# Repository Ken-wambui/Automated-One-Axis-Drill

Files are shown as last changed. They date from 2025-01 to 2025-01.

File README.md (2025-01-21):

One-Axis Drill: Design and Fabrication

**Introduction**
Welcome to the One-Axis Drill project! This repository contains the design, fabrication, and implementation details for a one-axis automated drilling machine. The project is intended for students, hobbyists, and professionals interested in mechanical design, CNC machinery, and automation.

Project Overview
The One-Axis Drill is designed to automate the drilling process along a single axis, providing precision and repeatability. It integrates mechanical, electrical, and software components to achieve its goal.

**Features**
Precision Drilling: Accurate drilling along a single axis.
Automated Control: Programmed movements for consistent results.
Customizable Design: Easy to modify for different applications.
Open Source: All design files and source code are available for free.

Acknowledgements
We would like to thank the open-source community for their invaluable resources and support.

Contact
For any questions or suggestions, feel free to open an issue in this repository or contact us at kentrevor2@gmail.com.

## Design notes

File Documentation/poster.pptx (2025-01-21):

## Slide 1

GROUP MEMBERS
1. Elizabeth Mugure
2. Fernado Ghati
3. Edwin Maina
4. John Kabi
5. Randy Baraka
6. Kenneth Wambui

Development Of One Axis Drill

MAIN OBJECTIVE
Development of a precise automated one axis drill and determine optimal drilling parameters.
Specific Objectives
- To design and simulate 3D model of the physical system.
- To develop project circuits and firmware to run sensors, actuators and peripherals.
- To carry out preliminary experiments and analysis to determine parameters for vibration mitigation

EXPECTED OUTCOMES
- To have an efficient firmware program for the working of sensors, actuators and peripherals for precise drilling operation
- To establish optimal drilling parameters from experimental and computational analysis.
- To visualize forces and vibration on the PMMA with respect to drill and feed speeds
- To mitigate vibrations, chatter and reduced risk of drill bit breakage and ensure efficient material removal during drilling.

22nd Aug, 2023

Supervisor: Dr. Titus Mulembo

ABSTRACT
Many industrial and medical applications call for perfectly drilled holes. The creation of an affordable, accurate drilling machine that can be used and records vibrations and forces exerted on the workpiece throughout the drilling process is essential. This research aims to improve bone drilling operations in medical applications by developing a one-axis drill system with a polymer workpiece. In order to mitigate vibration and reduce chatter or the risk of drill bit breakage, system monitoring is crucial for identifying the optimal parameters to use in system control. This involves utilizing analytical and computational resources to analyze PMMA behavior during drilling operations and guaranteeing effective material removal.

METHODOLOGY

1. Assessment of existing physical model

2. Development of program flowchart

Determination of drilling control parameters
Upload the program to the microcontroller
Run the experiment
Results and Data Collection
Evaluation and analysis

3. CAD Design in Solidworks

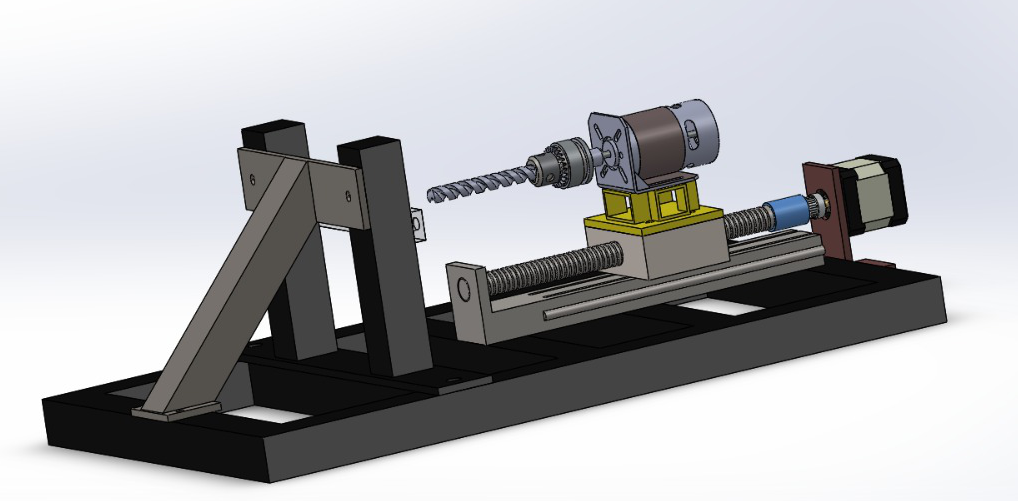
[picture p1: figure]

4. Importing to Matlab Simscape

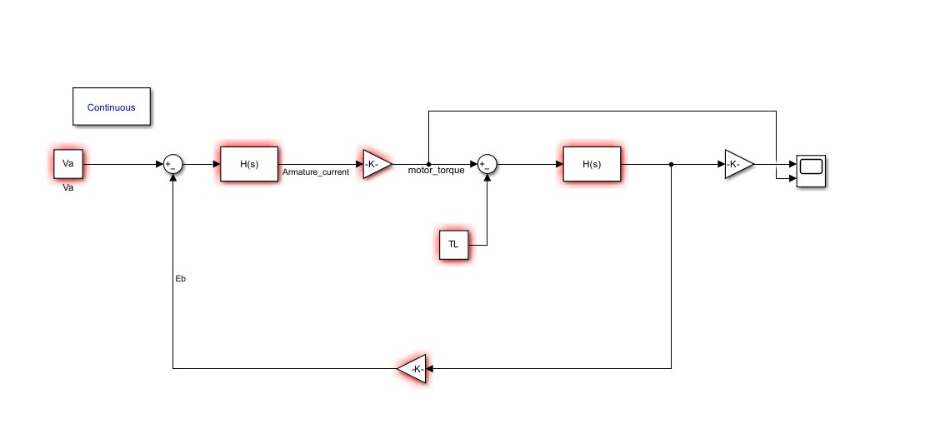
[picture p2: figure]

5. Finite element analysis in Ansys

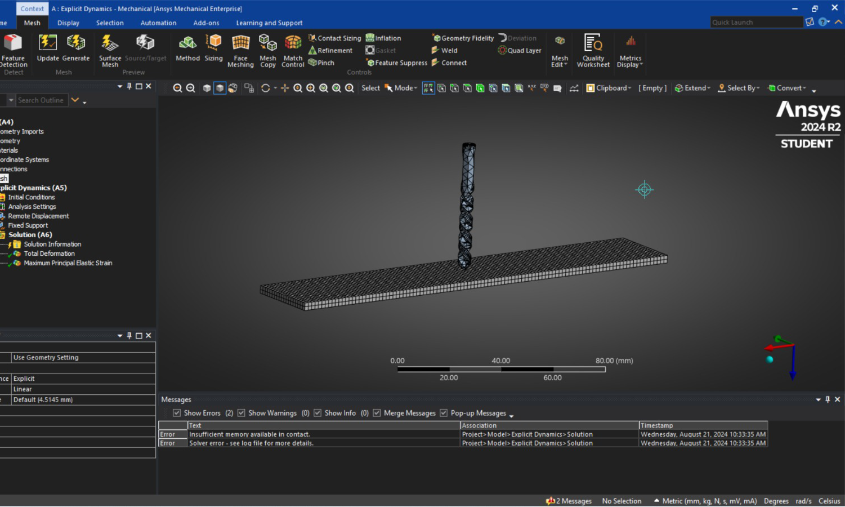
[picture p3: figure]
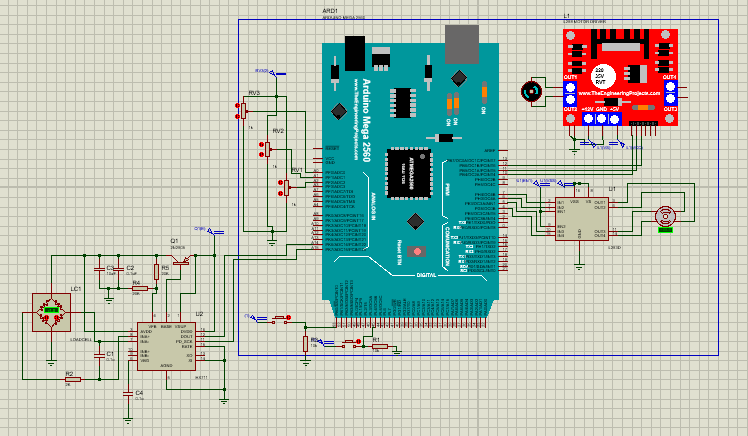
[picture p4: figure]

6. Programming and circuit simulation in Proteus, multisim

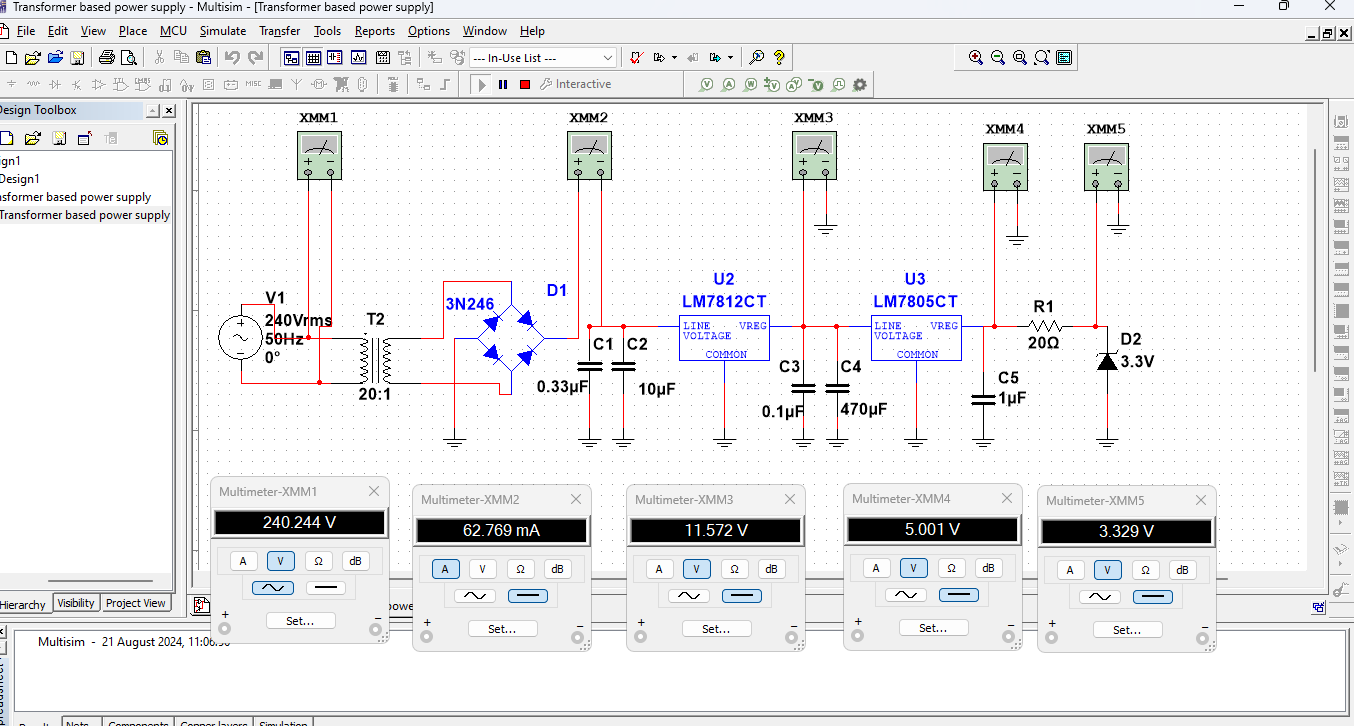
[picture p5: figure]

ACHIEVEMENTS

- Design of the project in Solidworks and simulation of the working motors in Matlab
- Circuit design in Proteus and simulations using Multism
- Development of working firmware program to read accurate real time sensor data and control dc and stepper motor.
- Gui Development for motor control and sensor data display

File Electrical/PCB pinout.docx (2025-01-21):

CIRCUIT PIN OUT

| Signal pin | Power pin
Stepper | B7(pul),A8(dir) | N/a
L298N dc motor control | B12(EN),B13(IN1),B14(IN2) | N/A
Vibration sensor | 10 | Pwr + gnd
Limit switch | A11 | Pwr + gnd
Temperature sensor | B8, B9
Load cell | B4, B5

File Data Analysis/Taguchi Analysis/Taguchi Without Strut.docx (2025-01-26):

WORKSHEET 1

Taguchi Analysis: Performance versus PWM, Feed Ratio, Diameter

Response Table for Signal to Noise Ratios

Larger is better

Level | PWM | Feed Ratio | Diameter
1 | 23.95 | 23.90 | 23.73
2 | 23.73 | 23.78 | 23.95
Delta | 0.23 | 0.13 | 0.23
Rank | 2 | 3 | 1

Response Table for Means

Level | PWM | Feed Ratio | Diameter
1 | 15.78 | 15.69 | 15.36
2 | 15.37 | 15.45 | 15.78
Delta | 0.41 | 0.23 | 0.42
Rank | 2 | 3 | 1

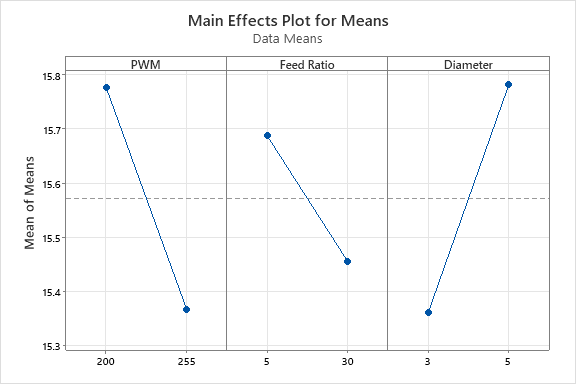
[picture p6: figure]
Main Effects Plot for Means
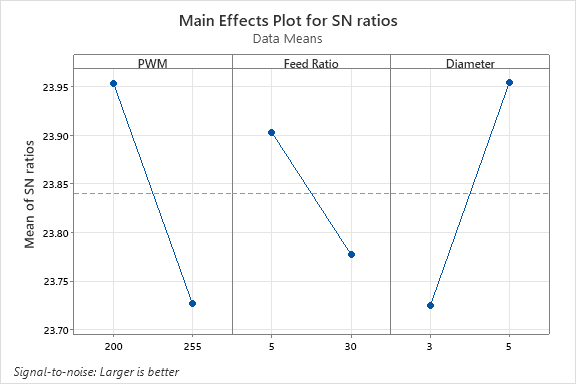
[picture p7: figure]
Main Effects Plot for SN ratios

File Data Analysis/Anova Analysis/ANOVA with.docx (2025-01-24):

Descriptive statistics

SHEET1

General Linear Model: Performance versus PWM, Feed Ratio,

WORKSHEET 1

General Linear Model: Performance versus PWM, Feed Ratio, Diameter

Method

Factor coding | (-1, 0, +1)

Factor Information

Factor | Type | Levels | Values
PWM | Fixed | 2 | 200, 255
Feed Ratio | Fixed | 2 | 5, 30
Diameter | Fixed | 2 | 3, 5

Analysis of Variance

Source | DF | Adj SS | Adj MS | F-Value | P-Value
PWM | 1 | 0.3351 | 0.3351 | 0.65 | 0.464
Feed Ratio | 1 | 0.1075 | 0.1075 | 0.21 | 0.671
Diameter | 1 | 0.3529 | 0.3529 | 0.69 | 0.453
Error | 4 | 2.0510 | 0.5127
Total | 7 | 2.8464

Model Summary

S | R-sq | R-sq(adj) | R-sq(pred)
0.716064 | 27.95% | 0.00% | 0.00%

Coefficients

Term | Coef | SE Coef | T-Value | P-Value | VIF
Constant | 15.571 | 0.253 | 61.50 | 0.000
PWM
200 | 0.205 | 0.253 | 0.81 | 0.464 | 1.00
Feed Ratio
5 | 0.116 | 0.253 | 0.46 | 0.671 | 1.00
Diameter
3 | -0.210 | 0.253 | -0.83 | 0.453 | 1.00

Regression Equation

Performance | = | 15.571 + 0.205 PWM_200 - 0.205 PWM_255 + 0.116 Feed Ratio_5 - 0.116 Feed Ratio_30 - 0.210 Diameter_3 + 0.210 Diameter_5

Diameter

Method

Factor coding | (-1, 0, +1)

Factor Information

Factor | Type | Levels | Values
PWM | Fixed | 2 | 200, 255
Feed Ratio | Fixed | 2 | 5, 30
Diameter | Fixed | 2 | 3, 5

Analysis of Variance

Source | DF | Adj SS | Adj MS | F-Value | P-Value
PWM | 1 | 0.74118 | 0.74118 | 1.03 | 0.367
Feed Ratio | 1 | 0.01561 | 0.01561 | 0.02 | 0.890
Diameter | 1 | 0.32520 | 0.32520 | 0.45 | 0.538
Error | 4 | 2.86852 | 0.71713
Total | 7 | 3.95051

Model Summary

S | R-sq | R-sq(adj) | R-sq(pred)
0.846835 | 27.39% | 0.00% | 0.00%

Coefficients

Term | Coef | SE Coef | T-Value | P-Value | VIF
Constant | 16.478 | 0.299 | 55.04 | 0.000
PWM
200 | 0.304 | 0.299 | 1.02 | 0.367 | 1.00
Feed Ratio
5 | 0.044 | 0.299 | 0.15 | 0.890 | 1.00
Diameter
3 | -0.202 | 0.299 | -0.67 | 0.538 | 1.00

Regression Equation

Perfomance | = | 16.478 + 0.304 PWM_200 - 0.304 PWM_255 + 0.044 Feed Ratio_5 - 0.044 Feed Ratio_30 - 0.202 Diameter_3 + 0.202 Diameter_5

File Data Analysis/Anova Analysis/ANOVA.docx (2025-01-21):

ANALYSIS OF VARIANCE(ANOVA)

1. Data collection

The goal of this analysis is to obtain optimal operating points for vibration and force on the workpiece and DC motor which provides rotary feed to the workpiece. We operate the DC under different conditions such as different drill bit sizes, different feed rate and drill speed to obtain optimal parameters for drilling PMMA material which mimic the properties of bones, which is a typical application of our project.

The two hypotheses in the experiment:

Null hypothesis: There is no significant difference in the mean quality of drilling across different levels of linear feed speed provided by the stepper motor and rotary speed determined by the DC motor.

Alternative hypothesis: There is a significant difference in the mean quality of drilling across different levels of linear feed speed provided by the stepper motor and rotary speed determined by the DC motor.

2. Interpretation of ANOVA results
- The p-values indicate the significance of each factor and their interactions.
- Feed rate has a p-value of <0.05, indicating that it has a significant effect on Optimal Drilling Performance.
- Drill Motor Speed also has a p-value of <0.05, suggesting a significant effect on Optimal Drilling Performance.
- Both the stepper motor speed and the drill motor speed independently significantly impact the quality or efficiency of the drilling process for PMMA material.
- The interaction between Stepper Motor Speed and Drill Motor Speed has a p-value of 0.516708, which is not statistically significant. Therefore, the interaction does not have a significant effect on Optimal Drilling Performance.
- The p- value of interaction between stepper motor speed and dc motor speed is greater than 0.5, thus we fail to reject null hypothesis; this means there is no significant difference in the mean quality of drilling across different levels of linear feed speed provided by the stepper motor and rotary speed determined by the DC motor. This means that the two variables can be controlled independent of each other to obtain best quality drilling.

From the analysis, the number of times the station is able to carry out a successful drilling operation is limited. The station exhibits a successful drilling operation when a slow feed rate and a fast drill speed is applied also when we have a smaller drill bits. Failure to drill can be attributed to the melting of PMMA and the sticking of the melted PMMA on the drill bit, making further drilling difficult. The new PMMA used melts when heated during heating. Using the current setup as it is, the optimal operating parameters is at Slow feed rate setting for stepper motor, where it operates at 21.6 rpm and for the dc motor, at 255PWM, which is equivalent to 9778rpm, which can be conditioned separately, with one of the variables held constant.

Recommendations

Since we’re using a relatively bigger motor, we should use a power supply that will provide supply of up to 24V for the DC motor to increase torque when drilling with bigger drill bits.

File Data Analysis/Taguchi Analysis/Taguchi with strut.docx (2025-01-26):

WORKSHEET 4

Taguchi Analysis: Perfomance versus RPM, Feed Ratio, Diameter

Response Table for Signal to Noise Ratios

Larger is better

Level | RPM | Feed Ratio | Diameter
1 | 24.49 | 24.35 | 24.22
2 | 24.17 | 24.31 | 24.44
Delta | 0.33 | 0.04 | 0.22
Rank | 1 | 3 | 2

Response Table for Means

Level | RPM | Feed Ratio | Diameter
1 | 16.78 | 16.52 | 16.28
2 | 16.17 | 16.43 | 16.68
Delta | 0.61 | 0.09 | 0.40
Rank | 1 | 3 | 2

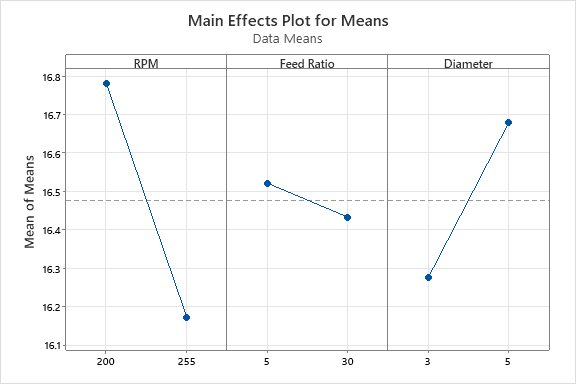
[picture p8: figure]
Main Effects Plot for Means
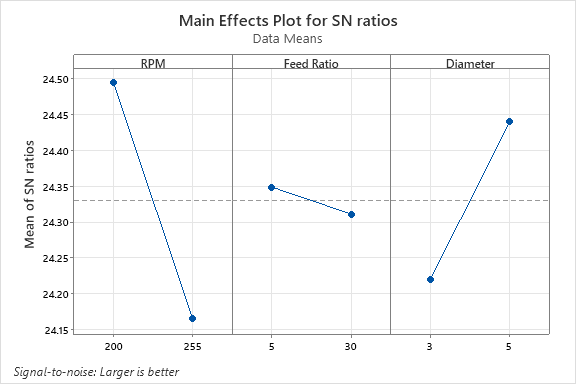
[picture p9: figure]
Main Effects Plot for SN ratios

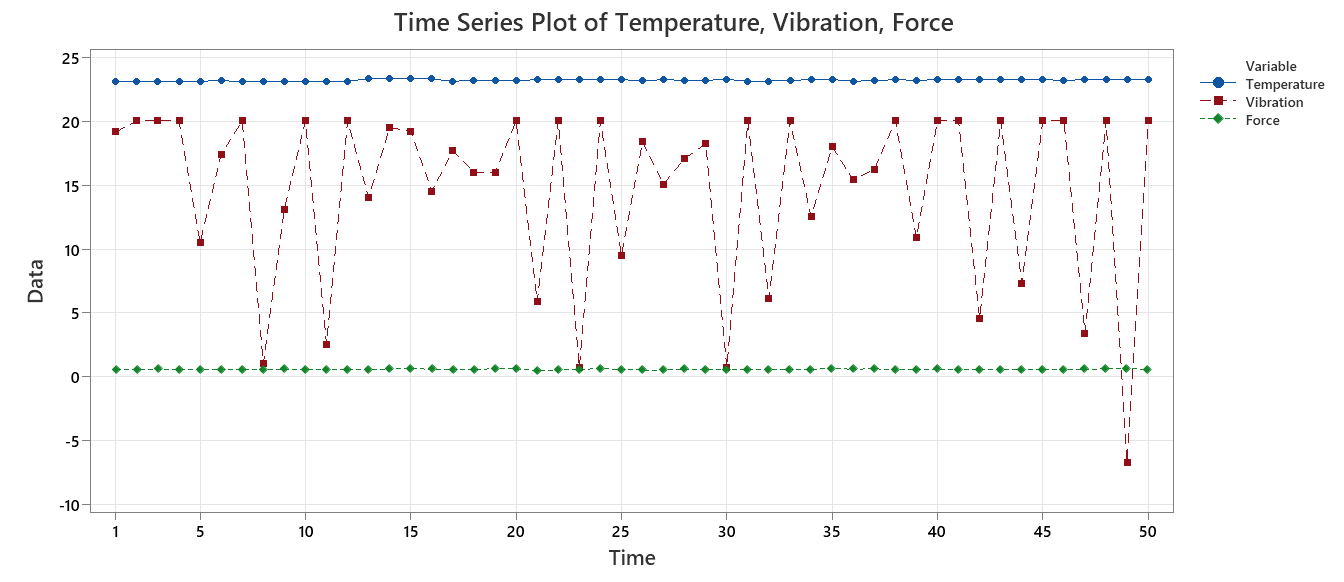
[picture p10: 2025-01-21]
Data Analysis/Graphs/Without Strut/5mm Bit/slow feed fast drill.png

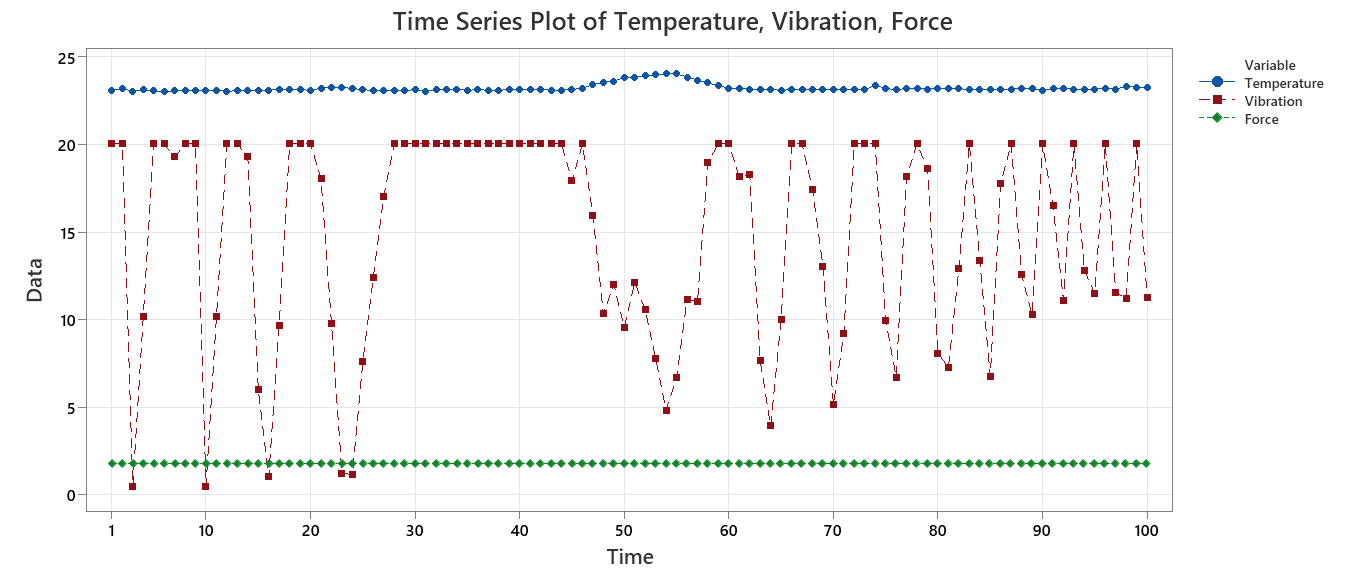
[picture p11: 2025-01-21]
Data Analysis/Graphs/Without Strut/3mm Bit/slow feed fast drill.png

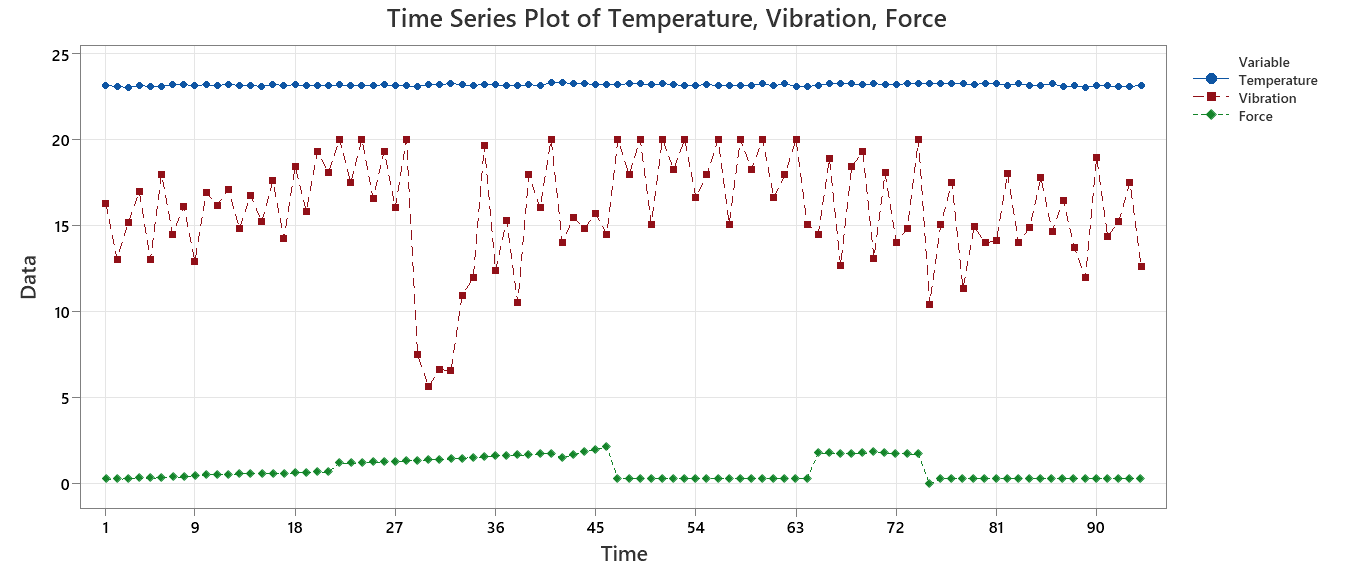
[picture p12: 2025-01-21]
Data Analysis/Graphs/Without Strut/3mm Bit/slow feed slow drill.png

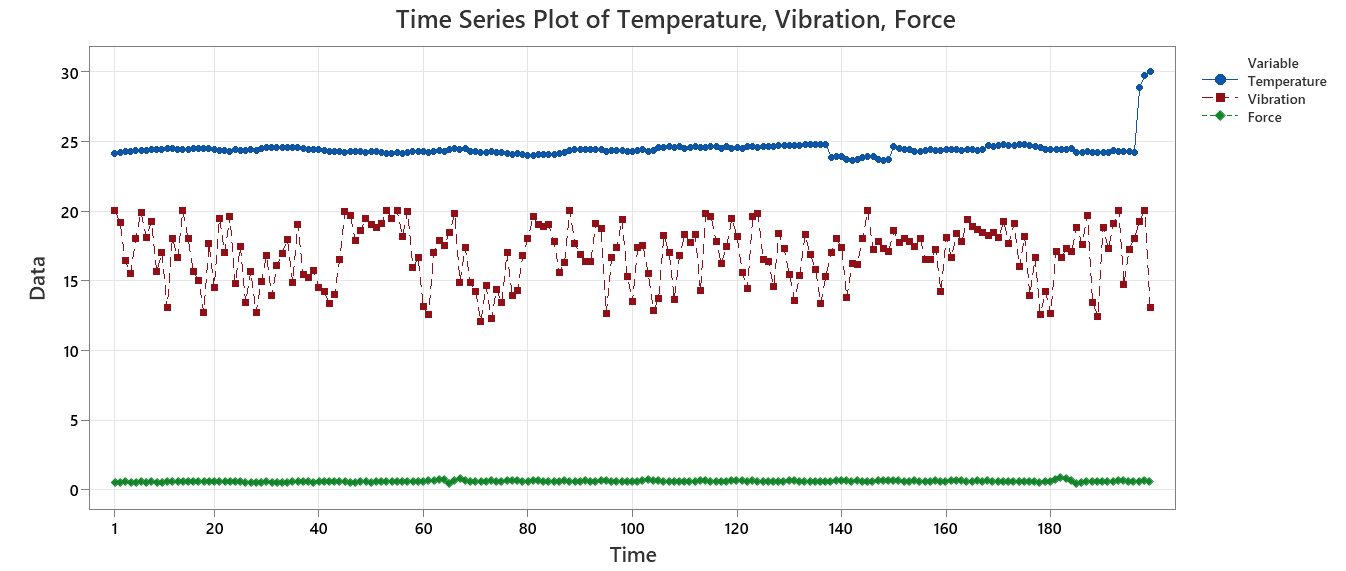
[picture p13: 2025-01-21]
Data Analysis/Graphs/With Strut/5mm Bit/slow feed fast drill.png

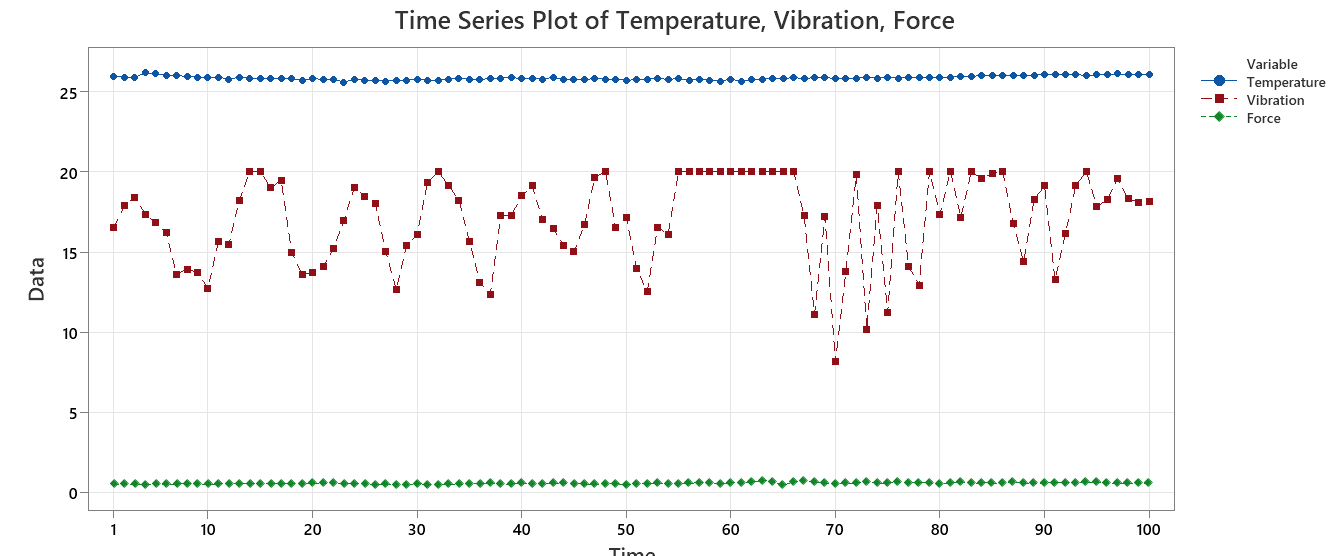
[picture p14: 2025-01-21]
Data Analysis/Graphs/With Strut/5mm Bit/Slow feed slow drill.png

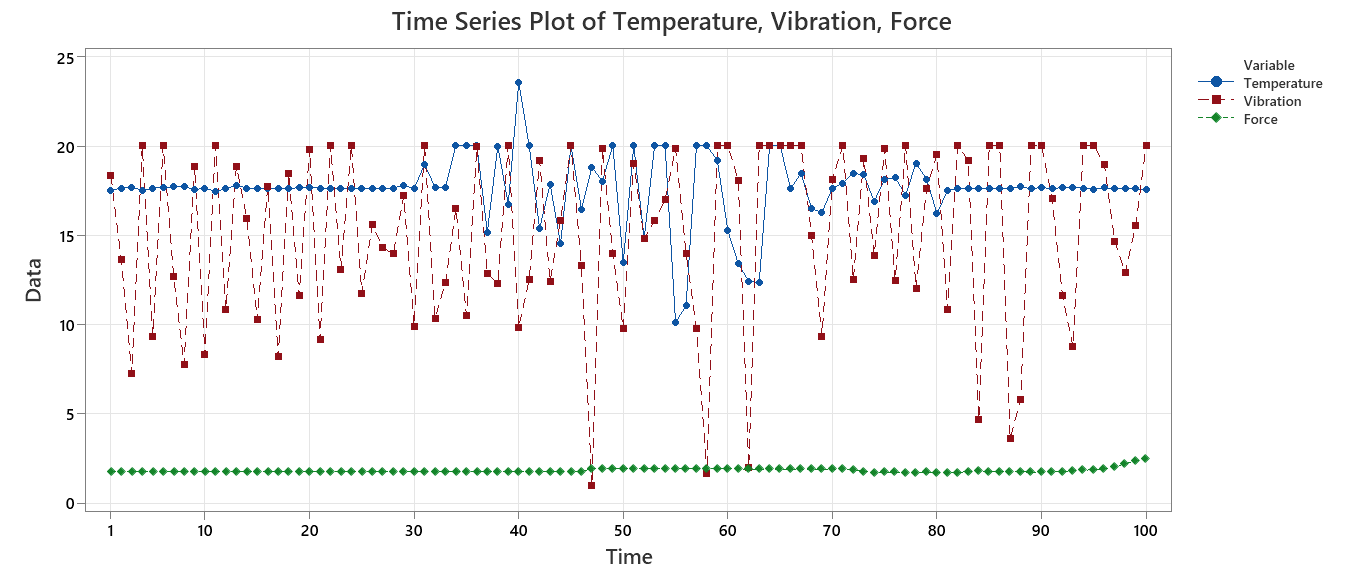
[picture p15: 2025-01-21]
Data Analysis/Graphs/With Strut/3mm Bit/fast feed slow drill.png

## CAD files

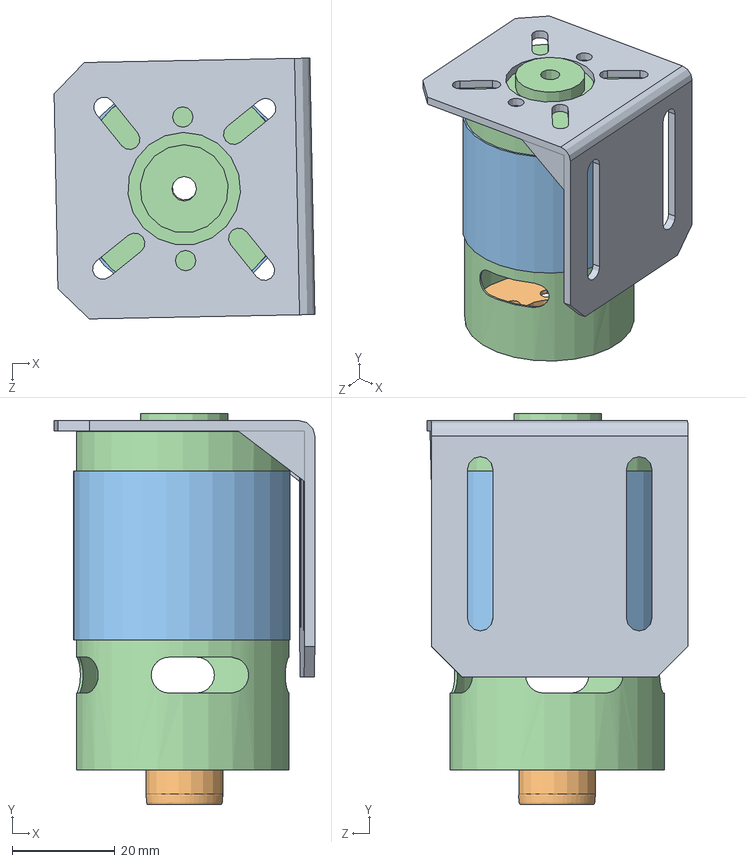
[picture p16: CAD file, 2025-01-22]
CAD/DC MOTOR/Assem2.SLDASM
50.9 x 76.2 x 50.9 mm
motor
case1
bottom
Motor Mount

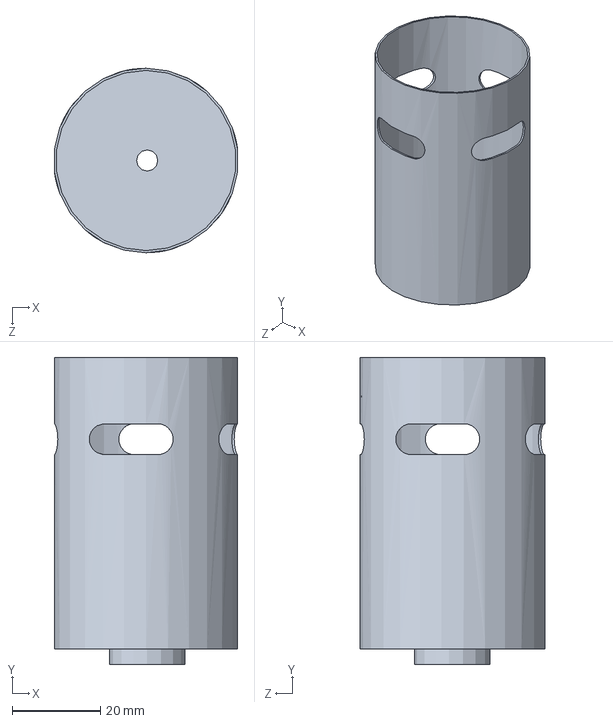
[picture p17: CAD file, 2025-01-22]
CAD/DC MOTOR/motor.SLDPRT
41.5 x 69.5 x 41.8 mm

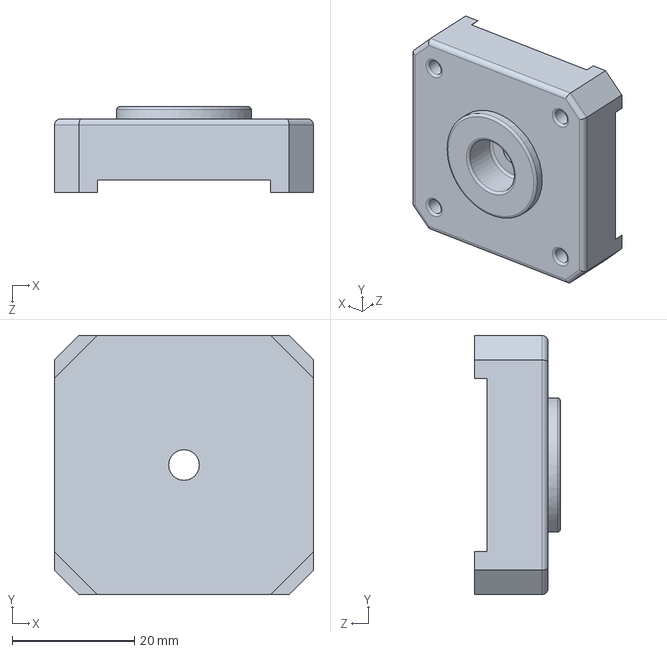
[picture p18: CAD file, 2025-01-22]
CAD/STEPPER MOTOR/Base Plate.SLDPRT
42.3 x 42.3 x 14.0 mm

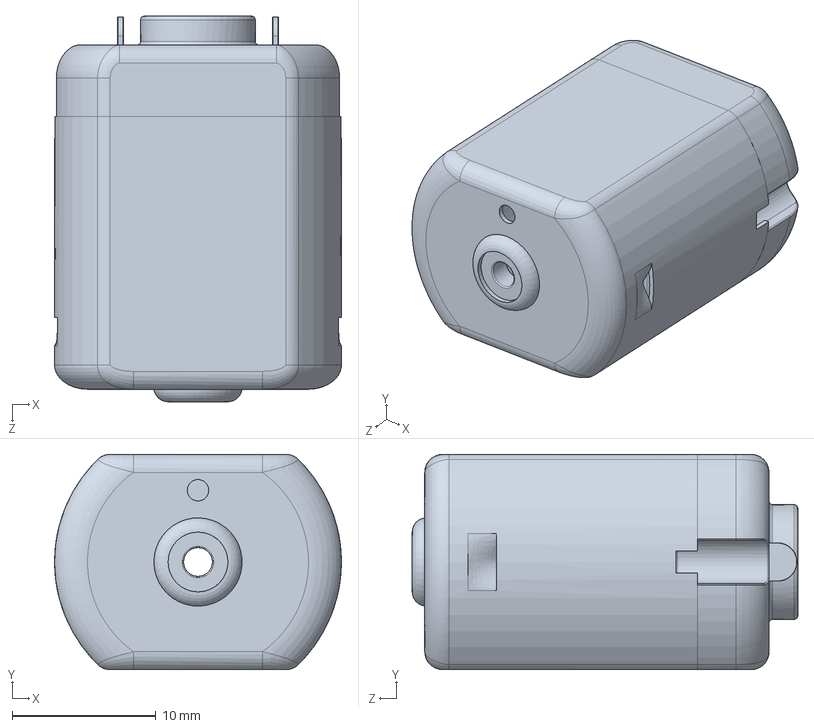
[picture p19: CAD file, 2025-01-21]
Simulations/Matlab/Dc motor/cassing.SLDPRT
20.0 x 15.0 x 26.9 mm

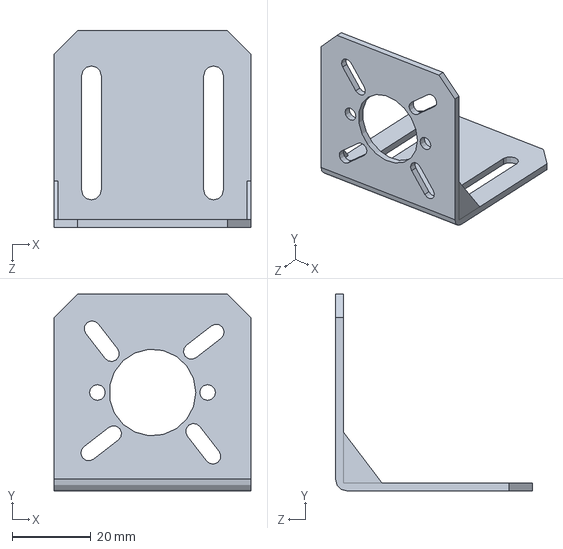
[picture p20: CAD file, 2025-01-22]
CAD/DC MOTOR/Motor Mount.SLDPRT
50.0 x 50.0 x 50.0 mm

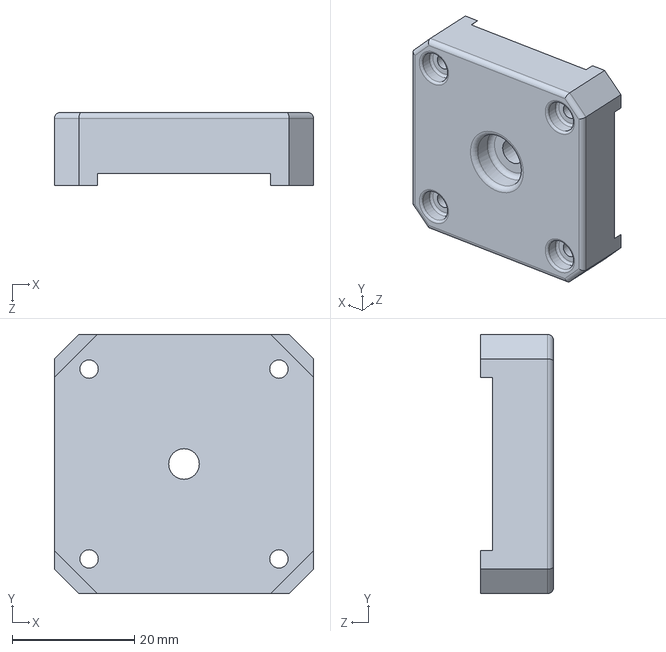
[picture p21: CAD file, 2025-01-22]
CAD/STEPPER MOTOR/Base step.SLDPRT
42.3 x 42.3 x 12.0 mm

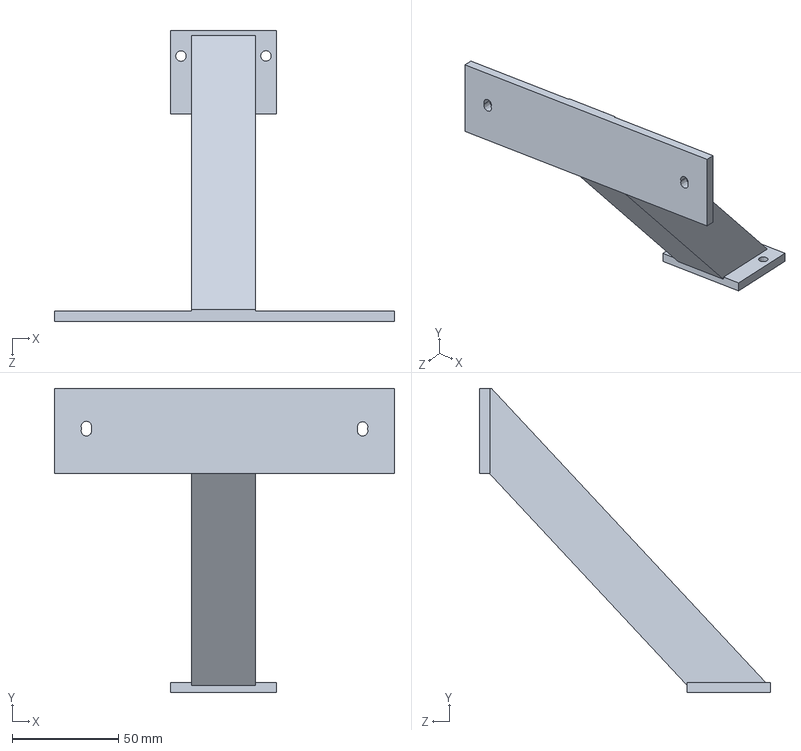
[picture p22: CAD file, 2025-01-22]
CAD/Strut.SLDPRT
160.0 x 143.3 x 136.9 mm

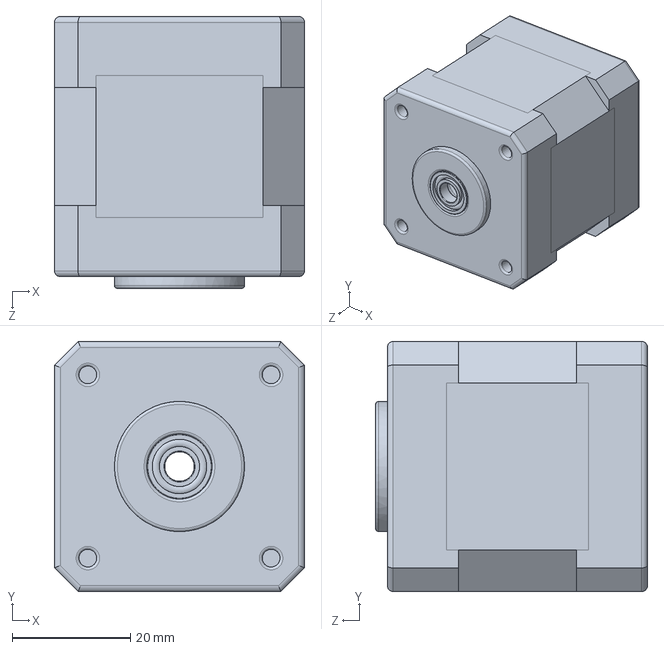
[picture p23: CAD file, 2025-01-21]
Simulations/Matlab/Stepper motor/case.SLDPRT
42.3 x 42.3 x 46.0 mm

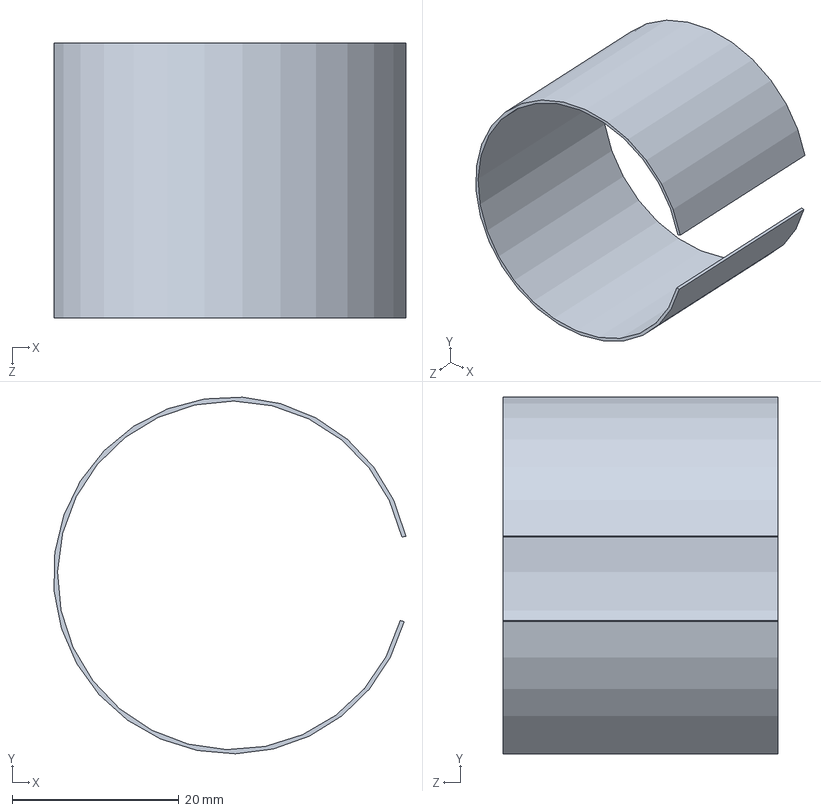
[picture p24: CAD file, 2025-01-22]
CAD/DC MOTOR/case1.SLDPRT
42.2 x 42.8 x 33.0 mm

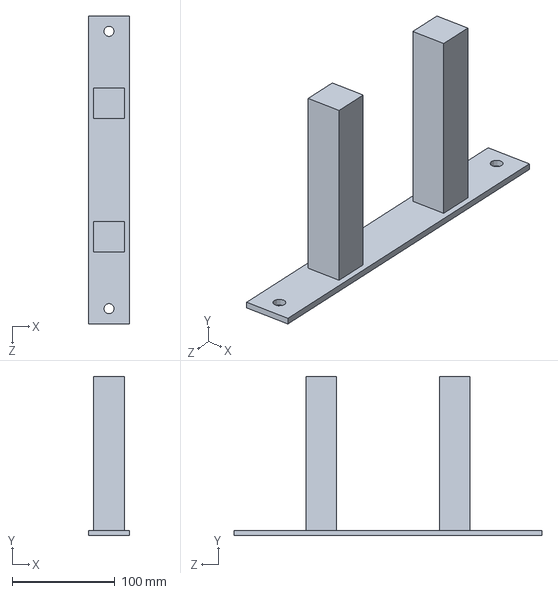
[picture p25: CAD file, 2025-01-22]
CAD/MOUNT.SLDPRT
40.0 x 155.0 x 300.0 mm

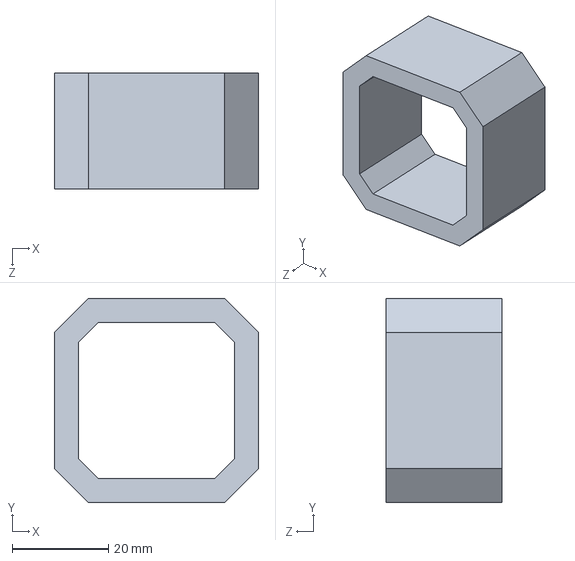
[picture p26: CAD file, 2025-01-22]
CAD/STEPPER MOTOR/Body.SLDPRT
42.3 x 42.3 x 24.0 mm

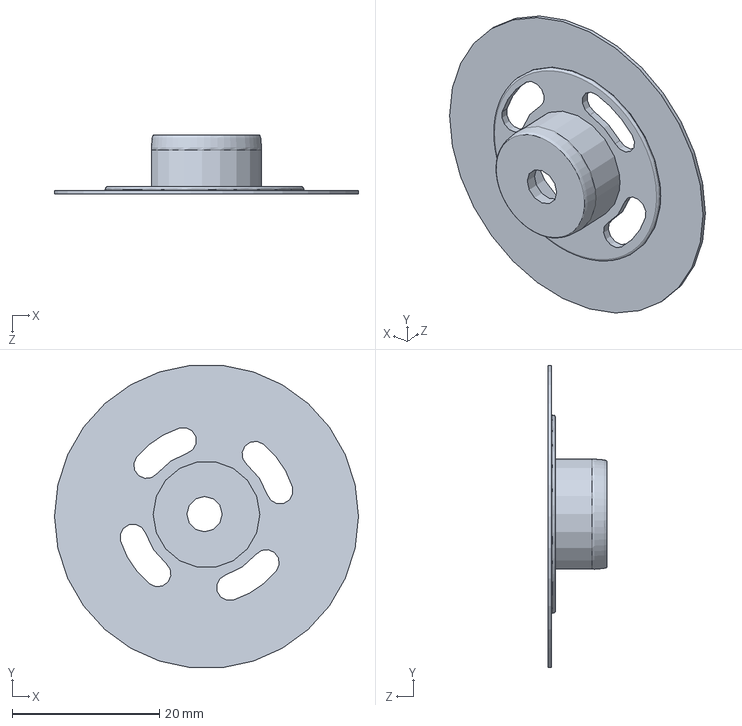
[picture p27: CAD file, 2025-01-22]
CAD/DC MOTOR/bottom.SLDPRT
41.3 x 41.1 x 8.00 mm

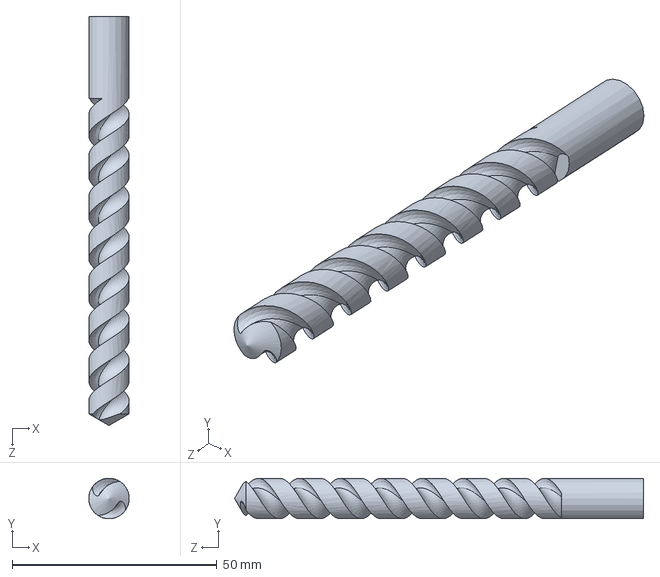
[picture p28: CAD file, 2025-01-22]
CAD/Drill Bit.SLDPRT
9.90 x 9.90 x 100.0 mm

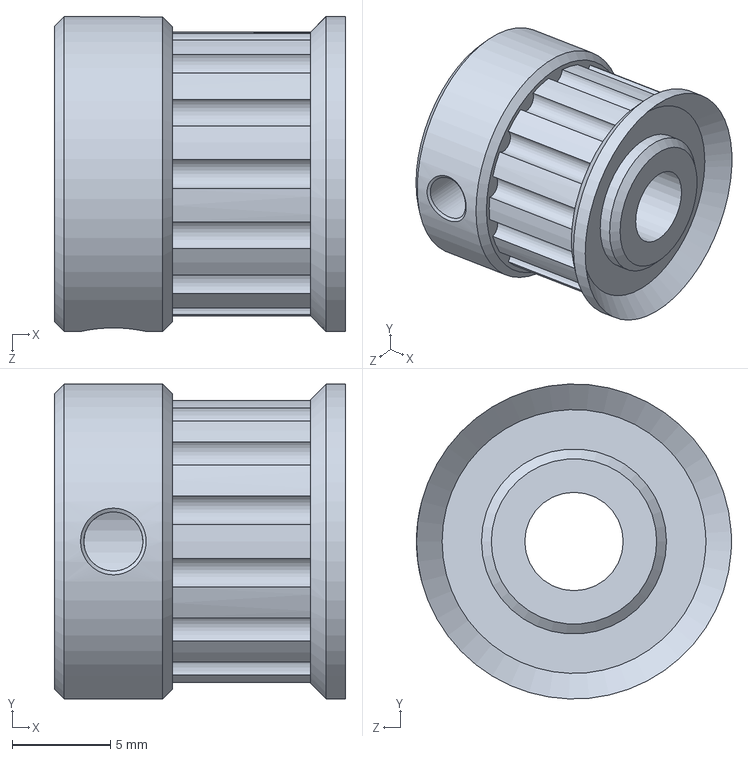
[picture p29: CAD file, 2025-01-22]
CAD/STEPPER MOTOR/Pulley.SLDPRT
14.8 x 16.0 x 16.0 mm

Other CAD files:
CAD/Drill Chuck.SLDASM
Simulations/Matlab/Stepper motor/sim assembley of stepper.SLDASM
CAD/STEPPER MOTOR/Stepper.SLDASM
Simulations/Matlab/Stepper motor/case_Default_sldprt.STEP
CAD/BASE.SLDPRT
CAD/Ball Screw FDV 32-5B2 .SLDPRT
CAD/Ball Screw FSW 25-4B1 .SLDPRT
CAD/Casing.SLDPRT
CAD/Chuck tooth.SLDPRT
CAD/DC MOTOR/casing.SLDPRT
CAD/DC MOTOR/pin.SLDPRT
CAD/DC MOTOR/rotary.SLDPRT
CAD/Drill Mount.SLDPRT
CAD/Lead screw Support.SLDPRT
CAD/M20 Bolt.SLDPRT
CAD/M20 Nut.SLDPRT
CAD/PMMA.SLDPRT
CAD/Rail.SLDPRT
CAD/Rollers.SLDPRT
CAD/STEPPER MOTOR/Axial Rod.SLDPRT
CAD/chuck outer.SLDPRT
CAD/chuck ring.SLDPRT
CAD/dc motor base mount.SLDPRT
CAD/lead screw.SLDPRT
Simulations/Matlab/Stepper motor/rotary part.SLDPRT
Simulations/Matlab/Stepper motor/rotary part_Default_sldprt.STEP

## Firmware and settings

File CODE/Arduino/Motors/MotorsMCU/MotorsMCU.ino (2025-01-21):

// Pin definitions
const int limitSwitchPin = 2;
const int stepPin = 3;
const int dirPin = 4;
const int enPin = 9;
const int enA = 7;
const int in1 = 6;
const int in2 = 5;

// Motor control variables
int speed = 0;
bool motorEnabled = false;
bool checkstop = false;
int stepperDirection = 1;
unsigned long previousMillis = 0;
const long interval = 50;
int timebt = 0;

// Define states for the state machine
enum State {
  IDLE,
  RUN_DC_MOTOR,
  RUN_STEPPER_MOTOR,
};

State currentState = IDLE;
unsigned long previousMillisDCMotor = 0;
unsigned long previousMillisStepperMotor = 0;

// Stepper motor feed rates (delay between steps)
const int stepperDelayHigh = 1000;  // Faster feed rate (smaller delay)
const int stepperDelayLow = 5000;   // Slower feed rate (larger delay)
int currentStepperDelay = stepperDelayLow; // Start with slow feed rate
int currentPosition = 0; // Track current position for feedback

// Setup serial communication
void setup() {
  Serial.begin(9600);      // Serial Monitor on Arduino Mega
  pinMode(enA, OUTPUT);
  pinMode(in1, OUTPUT);
  pinMode(in2, OUTPUT);
  pinMode(stepPin, OUTPUT);
  pinMode(dirPin, OUTPUT);
  pinMode(enPin, OUTPUT);
  digitalWrite(enPin, LOW);
  pinMode(limitSwitchPin, INPUT_PULLUP);
  digitalWrite(in1, LOW);
  digitalWrite(in2, LOW);

  Serial.println("Arduino Ready");
  while (!Serial.available() || Serial.readStringUntil('\n') != "Python Ready") {
    delay(100);
  }
}

void loop() {
  int limitSwitchState = digitalRead(limitSwitchPin);
  
  // Handle emergency stop at the start of each loop
  checkSerialForEmergencyStop();

  // Process serial commands
  if (Serial.available() > 0) {
    String command = Serial.readStringUntil('\n');
    command.trim();
    handleCommand(command);
  }

  // State machine logic
  switch (currentState) {
    case IDLE:
      if (motorEnabled) {
        currentState = RUN_DC_MOTOR;
      }
      break;
    case RUN_DC_MOTOR:
      runDCMotor(speed);
      if (!motorEnabled) {
        currentState = IDLE;
      }
      break;
    case RUN_STEPPER_MOTOR:
      runStepperMotor(timebt);
      currentState = IDLE;
      break;
  }

  // Limit switch handling
  if (limitSwitchState == HIGH) {
    handleLimitSwitch();
  }
  
  // Feedback to Python
  Serial.println("CURRENT SPEED:" + String(speed));
  Serial.println("CURRENT POSITION:" + String(currentPosition));
}

void checkSerialForEmergencyStop() {
  if (Serial.available() > 0) {
    String command = Serial.readStringUntil('\n');
    command.trim();
    if (command == "stopmachine") {
      emergencyStop();
    }
  }
}

void handleCommand(String command) {
  if (command == "stopmachine") {
    emergencyStop();
    Serial.println("STOPPED");
  } else if (command.startsWith("setSpeed")) {
    int newSpeed = command.substring(8).toInt();
    if (newSpeed >= 0 && newSpeed <= 255) {
      speed = newSpeed;
      motorEnabled = true;
      timebt = 10;
      Serial.println("SPEED SET TO: " + String(speed));
    } else {
      Serial.println("Invalid speed. Please enter a value between 0 and 255.");
    }
  } else if (command == "slowdrill") {
    speed = 100; // Set to a slower speed
    motorEnabled = true;
    timebt = 10;
    runDCMotor(speed);
    Serial.println("Slow drill mode activated");
  } else if (command == "fastdrill") {
    speed = 255; // Set to maximum speed
    motorEnabled = true;
    timebt = 10;
    runDCMotor(speed);
    Serial.println("Fast drill mode activated");
  } else if (command == "highFeedRate") {
    currentStepperDelay = stepperDelayHigh;
    Serial.println("High Feed Rate selected.");
  } else if (command == "slowFeedRate") {
    currentStepperDelay = stepperDelayLow;
    Serial.println("Slow Feed Rate selected.");
  }
}

void emergencyStop() {
  analogWrite(enA, 0);
  digitalWrite(enPin, HIGH);
  timebt = 0;
  speed = 0;
  motorEnabled = false;
  checkstop = true;
}

void runDCMotor(int speed) {
  digitalWrite(in1, LOW);
  digitalWrite(in2, HIGH);
  analogWrite(enA, speed); // Set the speed via PWM
}

void runStepperMotor(int steps) {
  digitalWrite(dirPin, LOW);
  digitalWrite(enPin, LOW);

  for (int i = 0; i < steps; i++) {
    digitalWrite(stepPin, HIGH);
    delayMicroseconds(currentStepperDelay);
    digitalWrite(stepPin, LOW);
    delayMicroseconds(currentStepperDelay);
    currentPosition++; // Increment position counter
  }
}

void handleLimitSwitch() {
  for (int m = 0; m < 5 && !checkstop; m++) {
    for (int i = 0; i < 600 && !checkstop; i++) {
      digitalWrite(dirPin, HIGH);
      digitalWrite(enPin, LOW);
      
      // Step the motor
      digitalWrite(stepPin, HIGH);
      delayMicroseconds(currentStepperDelay);
      digitalWrite(stepPin, LOW);
      delayMicroseconds(currentStepperDelay);
      currentPosition++;
      
      checkSerialForEmergencyStop(); // Check for emergency stop during operation
    }
  }
}

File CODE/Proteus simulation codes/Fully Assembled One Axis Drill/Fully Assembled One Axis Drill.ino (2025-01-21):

#include <Arduino.h>
#include "HX711.h"

// HX711 circuit wiring
const int LOADCELL_DOUT_PIN = 21;
const int LOADCELL_SCK_PIN = 20;
 HX711 scale;

const int buttonpinEND=45;
const int buttonpinSTART=53;
int buttonstateSTART=0;
int buttonstateEND=0;
const int enA = 10;  // Enable pin connected to L298 module
const int in1Pin = 11;    // Input 1 pin connected to L298 module
const int in2Pin = 12; 
int IN1 = 7;
int IN2= 6;
int IN3 = 5;
int IN4 = 4;
int delayTime =50;
int delayTime1= 100;
int delayTime2=200;

const int potXPin = A0; // Potentiometer for X-axis
const int potYPin = A1; // Potentiometer for Y-axis
const int potZPin = A2; // Potentiometer for Z-axis

void setup() {
    pinMode(buttonpinEND, INPUT);
   
    pinMode(enA, OUTPUT);
    pinMode(in1Pin, OUTPUT);
    pinMode(in2Pin, OUTPUT);
    pinMode(IN1, OUTPUT);
    pinMode(IN2, OUTPUT);
    pinMode(IN3, OUTPUT);
    pinMode(IN4, OUTPUT);
    Serial.begin (9600);
    digitalWrite(in1Pin,LOW);
    digitalWrite(in2Pin,LOW);
    Serial.begin(9600);
    setuploadcell();
}

void loop() {
  buttonstateEND=digitalRead(buttonpinEND);
    buttonstateSTART=digitalRead(buttonpinSTART);
    
  if(buttonstateEND==HIGH){
    //digitalWrite(ledpin,HIGH);
      getloadcelldata();
      getdataaccel();
       analogWrite(enA,0);
       digitalWrite(in1Pin, LOW);
       digitalWrite(in2Pin, LOW);
      digitalWrite(IN1, LOW);
      digitalWrite(IN2, HIGH);
      digitalWrite(IN3, LOW);
      digitalWrite(IN4, HIGH);
      delay(delayTime);
      digitalWrite(IN1, HIGH);
      digitalWrite(IN2, LOW);
      digitalWrite(IN3, LOW);
      digitalWrite(IN4, HIGH);
      delay(delayTime);
      digitalWrite(IN1, HIGH);
      digitalWrite(IN2, LOW);
      digitalWrite(IN3, HIGH);
      digitalWrite(IN4, LOW);
      delay(delayTime);
      digitalWrite(IN1, LOW);
      digitalWrite(IN2, HIGH);
      digitalWrite(IN3, HIGH);
      digitalWrite(IN4, LOW);
      delay(delayTime);
      delay(1000);
      
          digitalWrite(in1Pin, LOW);
          digitalWrite(in2Pin, LOW);
         digitalWrite(IN1, LOW);
          digitalWrite(IN2, LOW);
         digitalWrite(IN3, LOW);
         digitalWrite(IN4,LOW);  
         getloadcelldata();
         getdataaccel();
  }
  else if (buttonstateSTART==HIGH){
    getloadcelldata();
    getdataaccel();
      digitalWrite(IN1, HIGH);
      digitalWrite(IN2, LOW);
      digitalWrite(IN3, HIGH);
      digitalWrite(IN4, LOW);
      delay(delayTime1);
      digitalWrite(IN1, LOW);
      digitalWrite(IN2, HIGH);
      digitalWrite(IN3, HIGH);
      digitalWrite(IN4, LOW);
      delay(delayTime1);
      digitalWrite(IN1, LOW);
      digitalWrite(IN2, HIGH);
      digitalWrite(IN3, LOW);
      digitalWrite(IN4, HIGH);
      delay(delayTime1);
      digitalWrite(IN1, HIGH);
      digitalWrite(IN2, LOW);
      digitalWrite(IN3, LOW);
      digitalWrite(IN4, HIGH);
      delay(delayTime1);
      delay(1000);    
      getloadcelldata();
      getdataaccel();
      analogWrite(enA,255);
      digitalWrite(in1Pin, HIGH);
      digitalWrite(in2Pin, LOW);
      digitalWrite(IN1, HIGH);
      digitalWrite(IN2, LOW);
      digitalWrite(IN3, HIGH);
      digitalWrite(IN4, LOW);
      delay(delayTime2);
      digitalWrite(IN1, LOW);
      digitalWrite(IN2, HIGH);
      digitalWrite(IN3, HIGH);
      digitalWrite(IN4, LOW);
      delay(delayTime2);
      digitalWrite(IN1, LOW);
      digitalWrite(IN2, HIGH);
      digitalWrite(IN3, LOW);
      digitalWrite(IN4, HIGH);
      delay(delayTime2);
      digitalWrite(IN1, HIGH);
      digitalWrite(IN2, LOW);
      digitalWrite(IN3, LOW);
      digitalWrite(IN4, HIGH);
      delay(delayTime2);
   }
   else{
     getloadcelldata();
     getdataaccel();
      digitalWrite(IN1, LOW);
      digitalWrite(IN2, HIGH);
      digitalWrite(IN3, LOW);
      digitalWrite(IN4,HIGH);
      delay(delayTime);
      digitalWrite(IN1, HIGH);
      digitalWrite(IN2, LOW);
      digitalWrite(IN3, LOW);
      digitalWrite(IN4, HIGH);
      delay(delayTime);
      digitalWrite(IN1, HIGH);
      digitalWrite(IN2, LOW);
      digitalWrite(IN3, HIGH);
      digitalWrite(IN4, LOW);
      delay(delayTime);
      digitalWrite(IN1, LOW);
      digitalWrite(IN2,HIGH);
      digitalWrite(IN3, HIGH);
      digitalWrite(IN4, LOW);
      delay(delayTime);  
   }
}
   void getloadcelldata() {
  Serial.print("Weight in KG:\t");
  Serial.println(scale.get_units()/1000, 1);
 // delay(500);
}
void setuploadcell()
  {
  scale.begin(LOADCELL_DOUT_PIN, LOADCELL_SCK_PIN);
   Serial.println("Preparing and calibrating....");
  scale.read();
  scale.read_average(20);
  scale.get_value(5);
  scale.get_units(5), 1;
  scale.set_scale(36.059);
  scale.tare();
  scale.read();
  scale.get_value(5);
  scale.get_units(5), 1;
   Serial.println("Calibration complete");
  }

void getdataaccel(){
  // Read the potentiometer values
  int potXValue = analogRead(potXPin);
  int potYValue = analogRead(potYPin);
  int potZValue = analogRead(potZPin);

  // Map the potentiometer values to a range of -100 to +100
  float xDisplacement = map(potXValue, 0, 1023, -4, 4);
  float yDisplacement = map(potYValue, 0, 1023, -4, 4);
  float zDisplacement = map(potZValue, 0, 1023, -4, 4);

  // Print the displacements on the serial monitor
  Serial.print("X Displacement: ");
  Serial.print(xDisplacement);
  Serial.print("\tY Displacement: ");
  Serial.print(yDisplacement);
  Serial.print("\tZ Displacement: ");
  Serial.println(zDisplacement);

  delay(500); // Delay for smoother serial monitor output (adjust if needed)
}

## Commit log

2025-01-21 Data
    Uploaded Collected Data From various experiments in different conditions
    [Slow feed slow drill.xlsx, fast feed fast drill.xlsx, fast feed slow drill.xlsx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]
2025-01-21 Electrical Update
    Updated
    [Dc motor for simulink assembly 2.0.xml, case.SLDPRT, case_Default_sldprt.STEP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]
2025-01-21 Updated Codes And Ducumetation
    Provided Documents about the project and updated firmware codes for sensors and motors
2025-01-22 Updated CAD
    Updated for simulink multibody
    [Assem2.SLDASM, Axial Rod.SLDPRT, BASE.SLDPRT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]
2025-01-24 Data Analysis
    Further analysis for ANOVA and TAGUCHI DOE
    [With strut for TAGUCHI.xlsx, Without strut for TAGUCHI.xlsx]
2025-01-26 Taguchi DOE
    [datapwm0.csv, datapwm1.csv, datapwm2.csv]
